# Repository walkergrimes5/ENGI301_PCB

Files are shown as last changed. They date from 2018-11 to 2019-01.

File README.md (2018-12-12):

# ENGI301_PCB
PCB design files for ENGI 301 project 2

This project builds on the work I started earlier this year (2018). I am continuing to implement a Octavo PocketBeagle board as the primary flight controller for a 210mm quad copter. The PocketBeagle is not meant specifically for this task, and, as such, is missing several critical components required for flight and autonomous control. Specifically, the board lacks an accelerometer/gyroscope, a altimeter, a GPS connection point, and proper motor headers. The goal of this project is to create a cape for the PocketBeagle that upgrades functionality to include these missing components. The cape fits into the profile of the PocketBeagle and allows it to operate as a flight control board for a quad copter. Eventually, this system should be fully compatible with ArduPilot and be a cheap way to implement a small, autonomous drone.

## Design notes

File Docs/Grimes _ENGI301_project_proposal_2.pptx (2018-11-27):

## ENGI 301 QuadCopter PB Cape Proposal

19th November, 2018
Walker Grimes

## Background Information

  - I have already implemented the PB with Drone motors.
  - The PB lacks several critical systems that standard flight control boards have
    - Accelerometer
    - Gyroscope
    - Barometer
    - Altimeter
    - GPS
  - The goal of this project is to design a cape for the PB to meet these needs
- https://www.hackster.io/patrickpoirier51/pocketpilot-an-autopilot-based-on-the-25-pocketbeagle-1fa14b

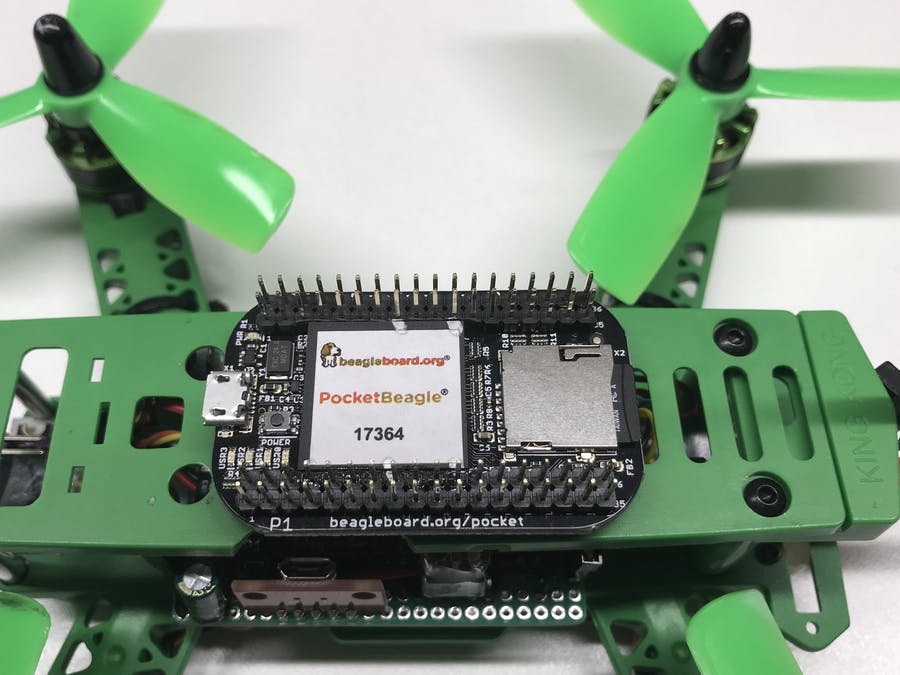
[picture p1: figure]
PocketPilot: An Autopilot Based on the $25 PocketBeagle®

Fig 1: Pocket Pilot

## Board Functionality

This board will serve two purposes:
  1. The PB doesn’t have the required instrumentation for proper flight control. This board will incorporate the three major chips (GPS, Accel/Gyro, Altimeter)
  2. The PB PWM pins are far apart and connecting the motors required a homemade breakout board. The cape will have a cluster of pins to simplify connections

## Functional Block Diagram

Motor Power Out

Vin

(GND,Vin,GND)

1300mah,14v, 4s LiPo Dynogy Battery

Accel/Gyro
MPU6050

PDB

5V BEC

PocketBeagle

I2C

6 Pin JST-SH (UART)

USB1 Port (P1_5,7,9,11,13,15)

100 mil 3 prong male headers
(GND,nc,sig)

Level
Shifter

3.3V

3.3V

1.8V

M1

M2

M3

M4

Altimeter

I2C

GPS

PWM

Micro USB

BR2205 Motors

## Mechanical Diagram

PocketBeagle

Cape

The cape will go on top of the PB
The connection will be accomplished by two 36 pin male headers on the bottom of the board matching the female headers on the board

Same Size

2.21”

1.38”

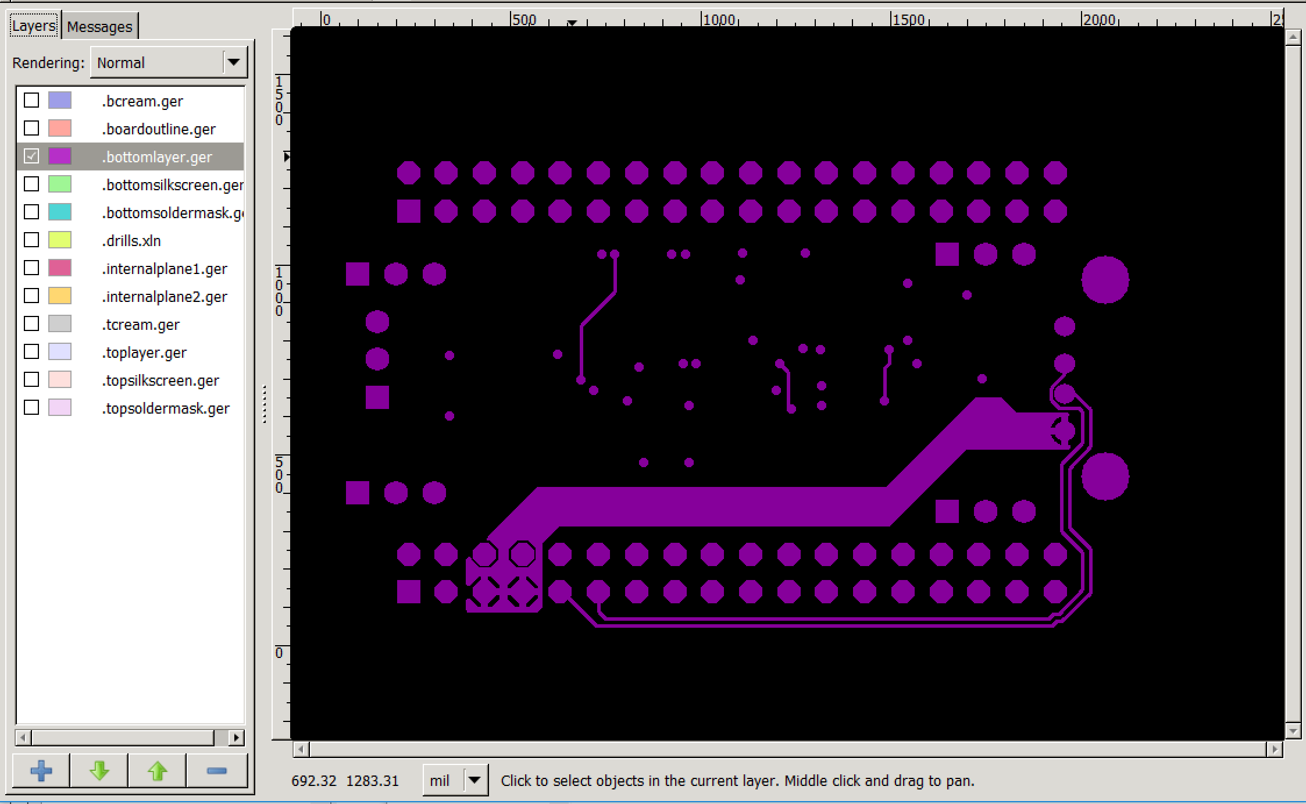
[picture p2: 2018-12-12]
Docs/Quad_Cape_Bottom_Layer.PNG

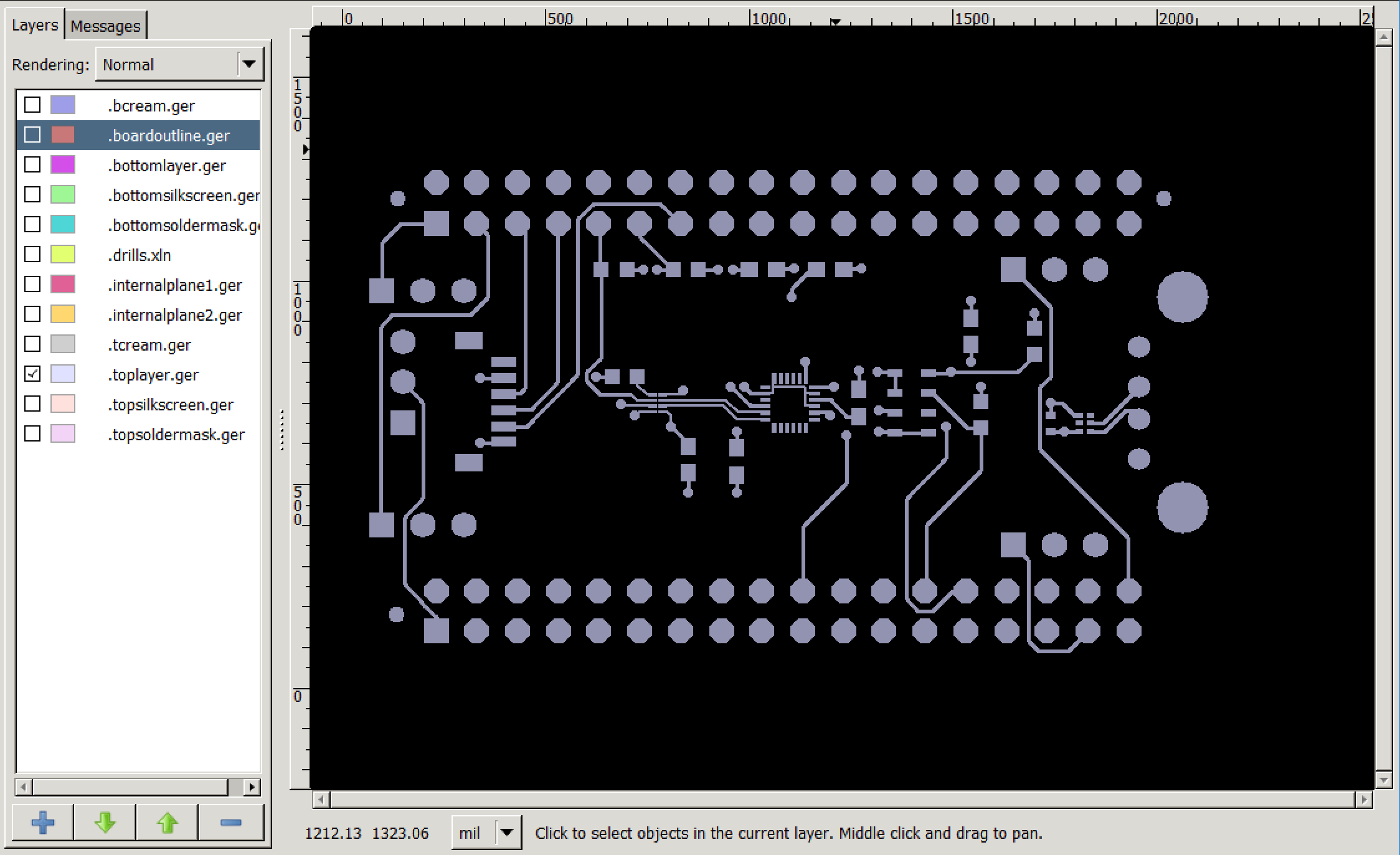
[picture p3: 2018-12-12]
Docs/Quad_Cape_Top_Layer.PNG

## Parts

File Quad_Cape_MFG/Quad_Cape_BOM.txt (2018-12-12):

Partlist exported from C:/Users/walke/Documents/Quad_Cape_ENGI301_PCB/EAGLE/Quad_Cape.sch at 12/11/2018 5:32 PM

Qty Value                       Device                      Package                                Parts                  Description                                               AVAILABILITY DESCRIPTION                                                                                            MF                MP          PACKAGE                   PRICE
1   .1uF                        CAPACITOR-(INCH)-0402       0402                                   C5                     Basic SMD ceramic capacitors                                                                                                                                                                                                               
6   0.1uF                       C_C0603                     C0603                                  C1, C2, C3, C4, C6, C7 Capacitor SMD.                                                                                                                                                                                                                             
5   10K                         R_R0603                     R0603                                  R1, R2, R3, R4, R5     RESISTOR, American symbol                                                                                                                                                                                                                  
5   3PIN_100MIL                 3PIN_100MIL                 3PIN_100MIL                            H1, H2, H3, H4, H5                                                                                                                                                                                                                                                
3   FIDUCIAL                    FIDUCIAL                    FIDUCIAL_40MIL                         FUD1, FUD2, FUD3                                                                                                                                                                                                                                                  
1   ICM-20948                   ICM-20948                   QFN40P300X300X105-25N                  U3                     Axis=3 Axis Gyro+3 Axis Accel+Compass. Pin For Pin With m Unavailable   9 Axis=3 Axis Gyro+3 Axis Accel+Compass. Pin For Pin With m                                           TDK InvenSense    ICM-20948   QFN-24 InvenSense         None 
1   MS5611-01BA03               MS5611-01BA03               MS5611-01BA03                          U2                                                                                                                                                                                                                                                                
1   POCKETBEAGLE                POCKETBEAGLE                POCKETBEAGLE                           U1                                                                                                                                                                                                                                                                
1   STRAWSON_EAGLE_LIB_JST_SH_6 STRAWSON_EAGLE_LIB_JST_SH_6 STRAWSON_EAGLE_LIB_JST_SH_6            6PIN1                                                                                                                                                                                                                                                             
1   TPD4S012DRY                 TPD4S012DRYR                SON-6(TI)-DRY                          IC1                                                                                                                                                                                                                                                               
1   TXS0102DQER                 TXS0102DQER                 VOLTAGETRANSLATOR_TXS0102DQER          U4                     IC TRANSLATOR VOLTAGE 8-X2SON                             Unavailable   2-Bit Bidirectional Voltage-Level Shifter for Open-Drain and Push-Pull Application 8-X2SON -40 to 85  Texas Instruments TXS0102DQER XFDFN-8 Texas Instruments None 
1   USB                         GHI2_USB_HOST_W/CHASSIS_GND GHI2_USB_HOST_HORIZONTAL_W/CHASSIS_GND X1

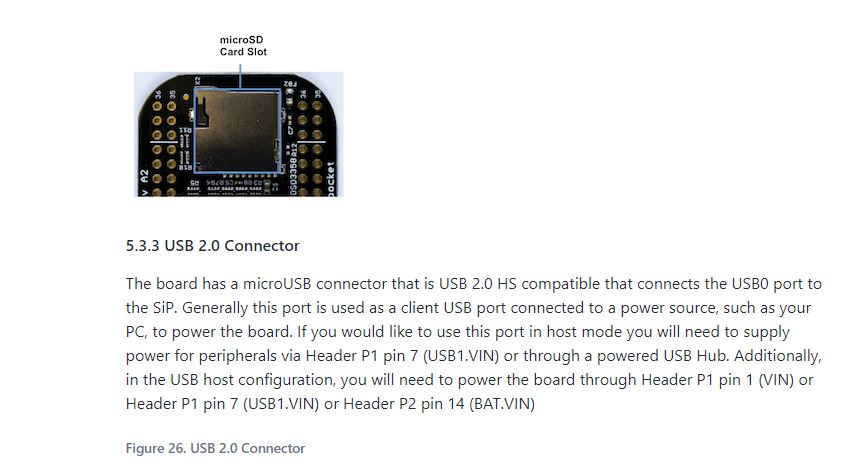
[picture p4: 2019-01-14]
Component References/USB PB.JPG

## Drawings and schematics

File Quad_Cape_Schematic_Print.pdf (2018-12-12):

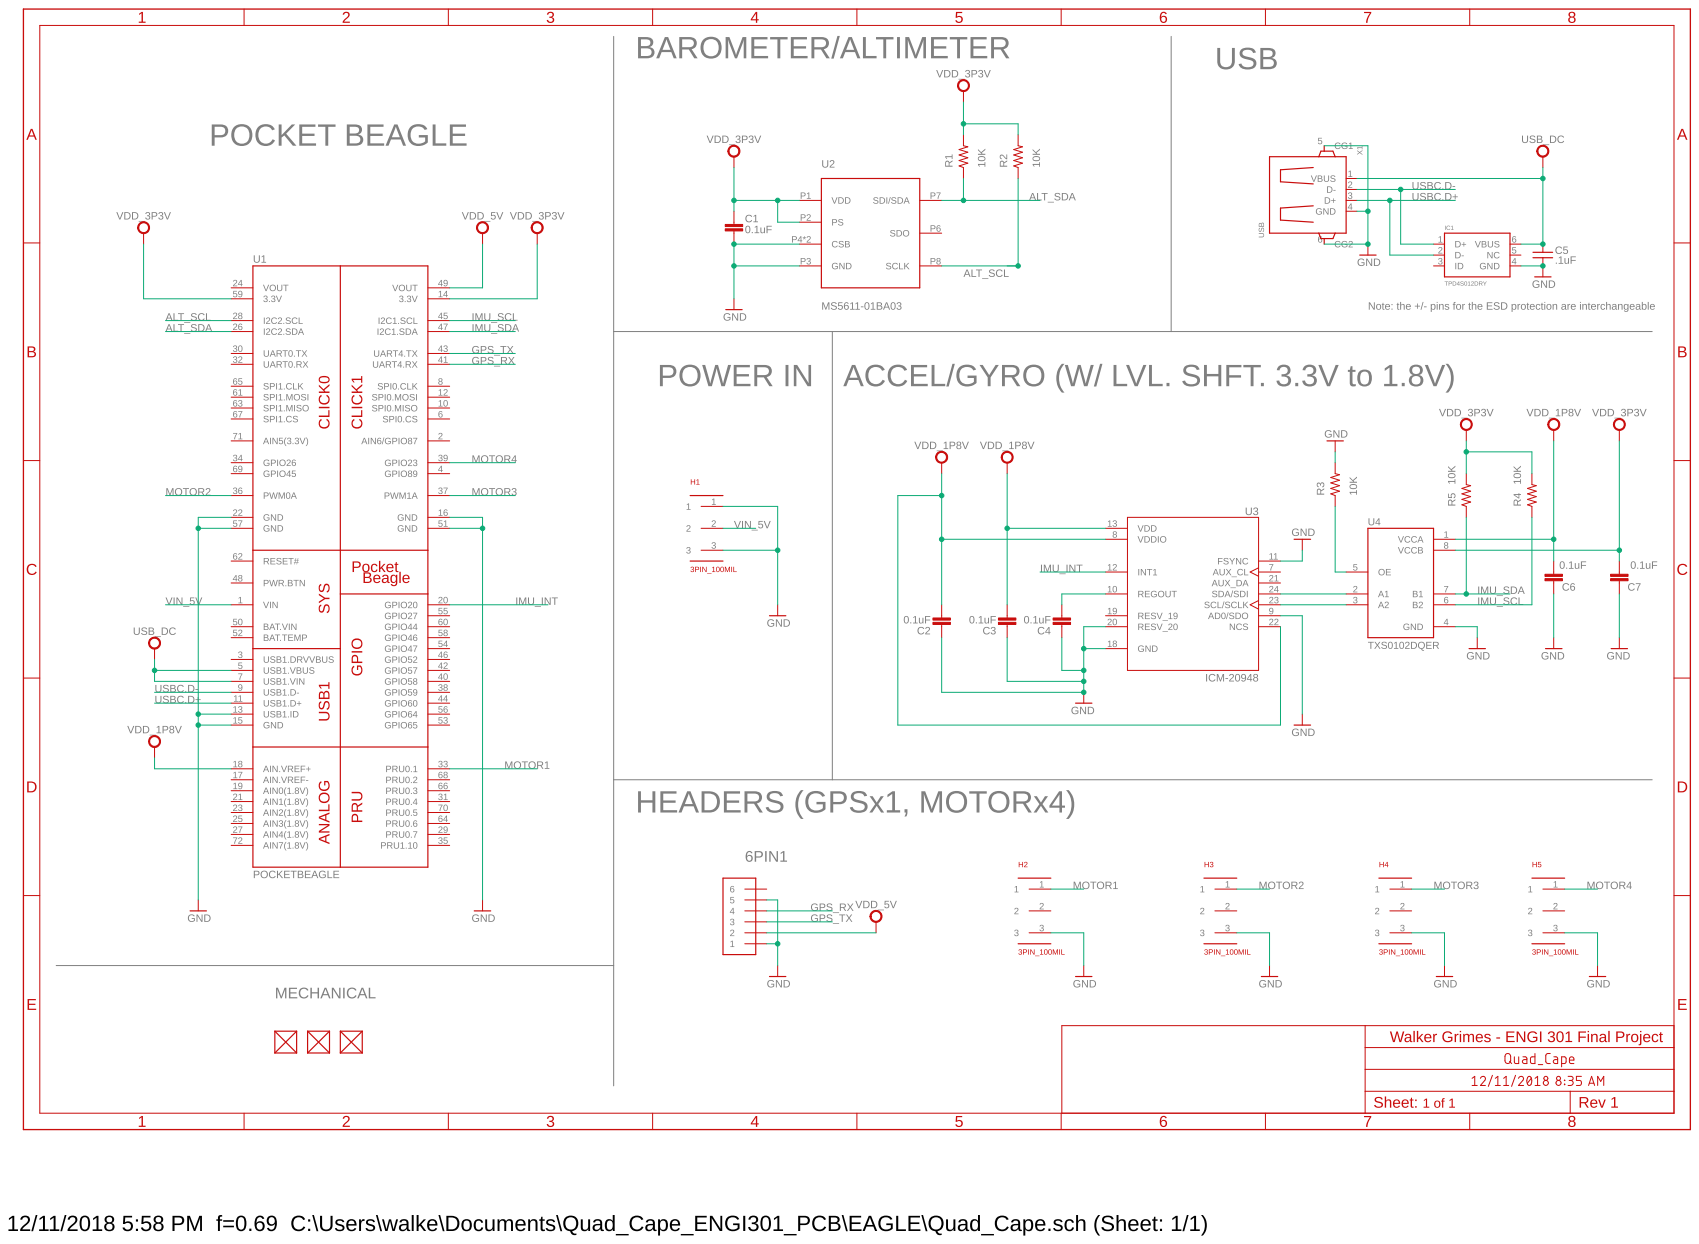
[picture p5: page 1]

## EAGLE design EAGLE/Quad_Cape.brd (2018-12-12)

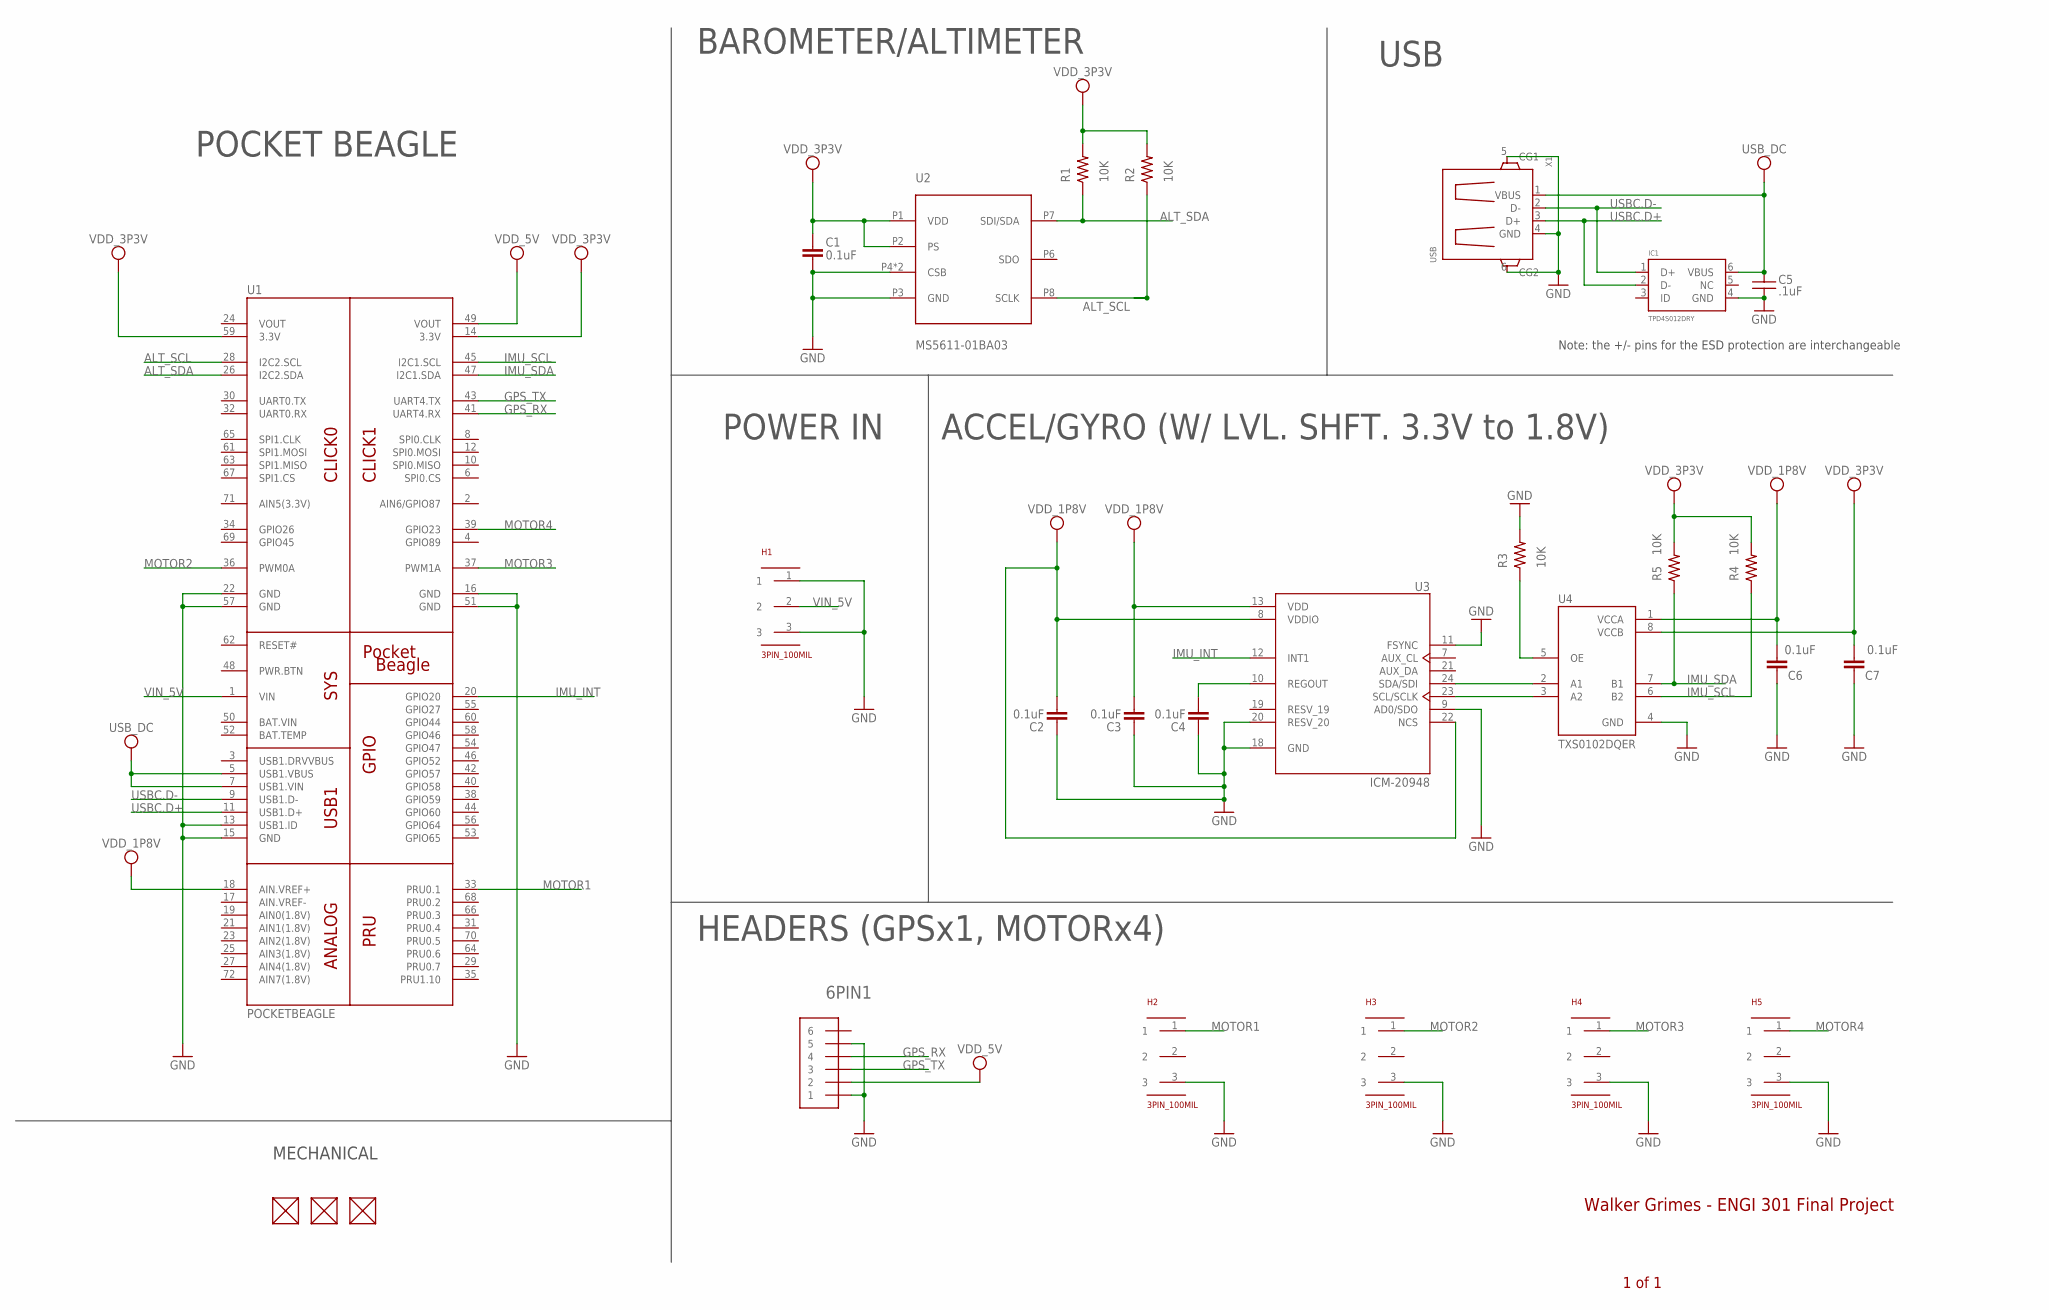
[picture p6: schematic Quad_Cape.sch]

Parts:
6PIN1: STRAWSON_EAGLE_LIB_JST_SH_6
C1, C2, C3, C4, C6, C7: 0.1uF; C0603
C5: .1uF; 0402
FUD1, FUD2, FUD3: FIDUCIAL; FIDUCIAL_40MIL
H1, H2, H3, H4, H5: 3PIN_100MIL
IC1: TPD4S012DRY; SON-6(TI)-DRY
R1, R2, R3, R4, R5: 10K; R0603
U1: POCKETBEAGLE
U2: MS5611-01BA03
U3: ICM-20948; QFN40P300X300X105-25N
U4: TXS0102DQER; VOLTAGETRANSLATOR_TXS0102DQER
X1: USB; GHI2_USB_HOST_HORIZONTAL_W/CHASSIS_GND

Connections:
ALT_SCL: R2.1, U1.28 (I2C2.SCL), U2.P8 (SCLK)
ALT_SDA: R1.1, U1.26 (I2C2.SDA), U2.P7 (SDI/SDA)
BAT.VIN: U1.50 (BAT.VIN)
GND: 6PIN1.1, 6PIN1.5, C1.2, C2.1, C3.1, C4.1, C5.2, C6.1, C7.1, H1.1, H1.3, H2.3, H3.3, H4.3, H5.3, IC1.4 (GND), R3.2, U1.13 (USB1.ID), U1.15 (GND), U1.16 (GND), U1.22 (GND), U1.51 (GND), U1.57 (GND), U2.P3 (GND), U2.P4 (CSB), U2.P5 (CSB), U3.9 (AD0/SDO), U3.11 (FSYNC), U3.18 (GND), U3.20 (RESV_20), U4.4 (GND), X1.4 (GND), X1.5 (CG1), X1.6 (CG2)
GPS_RX: 6PIN1.4, U1.41 (UART4.RX)
GPS_TX: 6PIN1.3, U1.43 (UART4.TX)
IMU_INT: U1.20 (GPIO20), U3.12 (INT1)
IMU_SCL: R4.1, U1.45 (I2C1.SCL), U4.6 (B2)
IMU_SDA: R5.1, U1.47 (I2C1.SDA), U4.7 (B1)
MOTOR1: H2.1, U1.33 (PRU0.1)
MOTOR2: H3.1, U1.36 (PWM0A)
MOTOR3: H4.1, U1.37 (PWM1A)
MOTOR4: H5.1, U1.39 (GPIO23)
unnamed: C4.2, U3.10 (REGOUT)
unnamed: R3.1, U4.5 (OE)
unnamed: U3.23 (SCL/SCLK), U4.3 (A2)
unnamed: U3.24 (SDA/SDI), U4.2 (A1)
USBC.D+: IC1.2 (D-), U1.11 (USB1.D+), X1.3 (D+)
USBC.D-: IC1.1 (D+), U1.9 (USB1.D-), X1.2 (D-)
USB_DC: C5.1, IC1.6 (VBUS), U1.5 (USB1.VBUS), U1.7 (USB1.VIN), X1.1 (VBUS)
VDD_1P8V: C2.2, C3.2, C6.2, U1.18 (AIN.VREF+), U3.8 (VDDIO), U3.13 (VDD), U3.22 (NCS), U4.1 (VCCA)
VDD_3P3V: C1.1, C7.2, R1.2, R2.2, R4.2, R5.2, U1.14 (3.3V), U1.59 (3.3V), U2.P1 (VDD), U2.P2 (PS), U4.8 (VCCB)
VDD_5V: 6PIN1.2, U1.49 (VOUT)
VIN_5V: H1.2, U1.1 (VIN)
VOUT: U1.24 (VOUT)

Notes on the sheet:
Walker Grimes - ENGI 301 Final Project
HEADERS (GPSx1, MOTORx4)
BAROMETER/ALTIMETER
USB
ACCEL/GYRO (W/ LVL. SHFT. 3.3V to 1.8V)
POCKET BEAGLE
1 of 1
POWER IN
MECHANICAL
Note: the +/- pins for the ESD protection are interchangeable

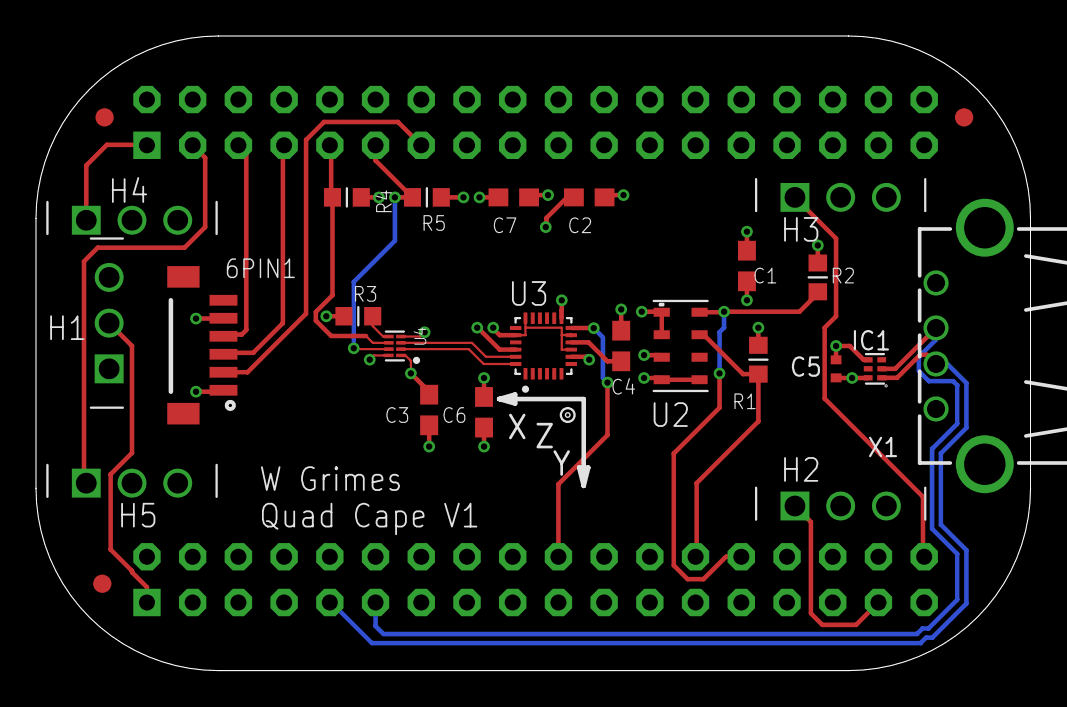
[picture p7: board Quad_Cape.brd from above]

Board: 4 copper layers, 55.3 x 35.3 mm, 28 parts (0 on the bottom side), 23 nets.

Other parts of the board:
U$5: XYZ_BIG

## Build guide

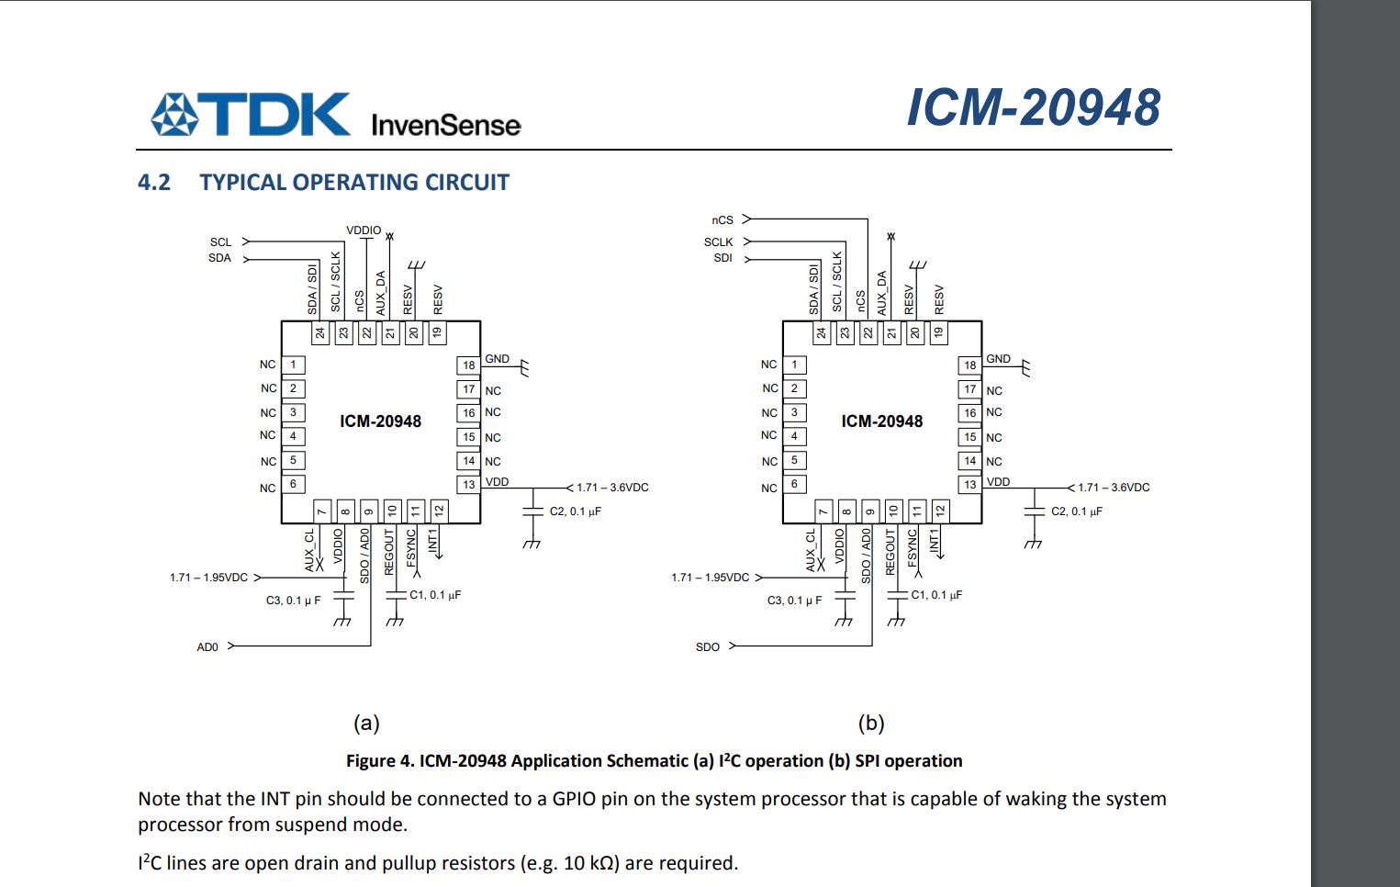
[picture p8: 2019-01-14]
Component References/IMU Wiring.JPG

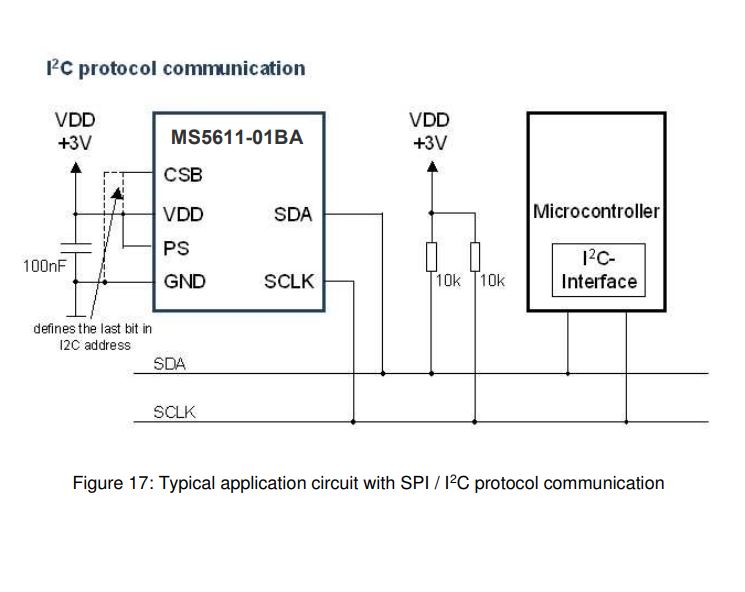
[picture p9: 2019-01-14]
Component References/ALT Wiring.JPG

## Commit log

2018-12-11 BOM and board updates
    [Quad_Cape.brd, Quad_Cape.csv, Quad_Cape.sch]
2018-12-11 Final changes for V1 board
    [Quad_Cape.brd, Quad_Cape.csv, Quad_Cape.sch]
2018-12-12 Added documentation to project
    Added Gerber files
    [Quad_Cape.brd, Quad_Cape.csv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]
2018-12-12 Final design tweaks and documentation
    [Quad_Cape.brd]
2019-01-14 Add files via upload
    Added additional reference material
